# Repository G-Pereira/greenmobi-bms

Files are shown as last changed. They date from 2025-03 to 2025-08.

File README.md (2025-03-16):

# GreenMobi BMS - A BMS board compatible with the VESC BMS firmware

The [VESC BMS board system is under closed development](https://vesc-project.com/node/311) at the time of this writing although the BMS firmware is publicly available so this project consists on a VESC compatible BMS board that is able to run [VESC BMS firmware](https://github.com/vedderb/vesc_express).

This project is under development and the board is not yet ready. [KiCAD](https://www.kicad.org/) is being used for the board's design and contributions are welcome.

[**Join us on discord**](https://discord.gg/AxKemSxhaV)

## Desing approach

Since there is not yet a opensource design of a VESC fully compatible BMS this board is being designed with ease of development in mind so it can be used as a reference design to contribute directly to the VESC project and extend its potential. So the following principles are followed:

- Popular and easy to source connectors are used (JST PH, screw terminals, etc) even if in most end uses it would be better to have weatherproof panel connectors.
- SMD packages optimized for JLC assembly or PnP on premises (down to 0402 passives).
- Up to 32S supported

Here it is a block diagram of the design:

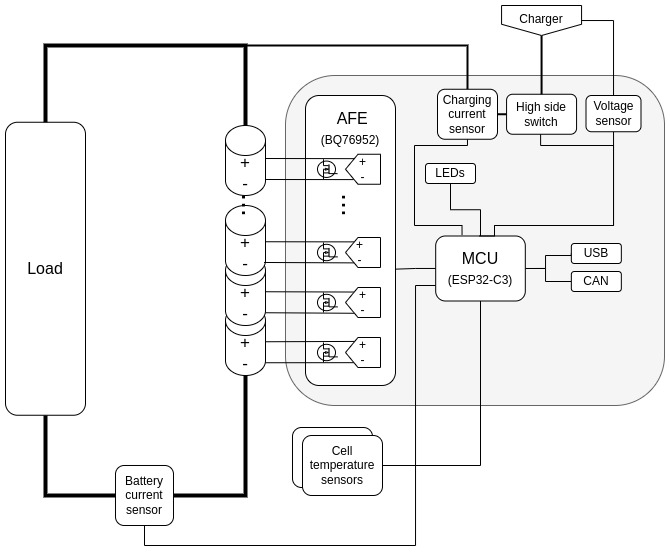
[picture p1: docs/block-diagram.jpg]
Block diagram


## Contributions

Since the design is at a schematic phase, it would be helpful if you can review the board's schematic to look for misconnections and erros using any of the given ICs. However, any other kind of productive feedback and work is welcome. Be sure to read the [design approach](#desing-approach) so your contributions match the goals of the project.

### Schematic PDF

To get the latest PDF version of the shematic go to GitHub Actions and download the artifacts of the latest workflow run.

## Credits

This project is meant to be interoperable with the VESC, which is a [registred trademark](https://vesc-project.com/trademark_policies), held by Benjamin Vedder and the BMS firmware and its hardware design hints that are in it that this designs follows are of Benjamin Vedder's authoring.

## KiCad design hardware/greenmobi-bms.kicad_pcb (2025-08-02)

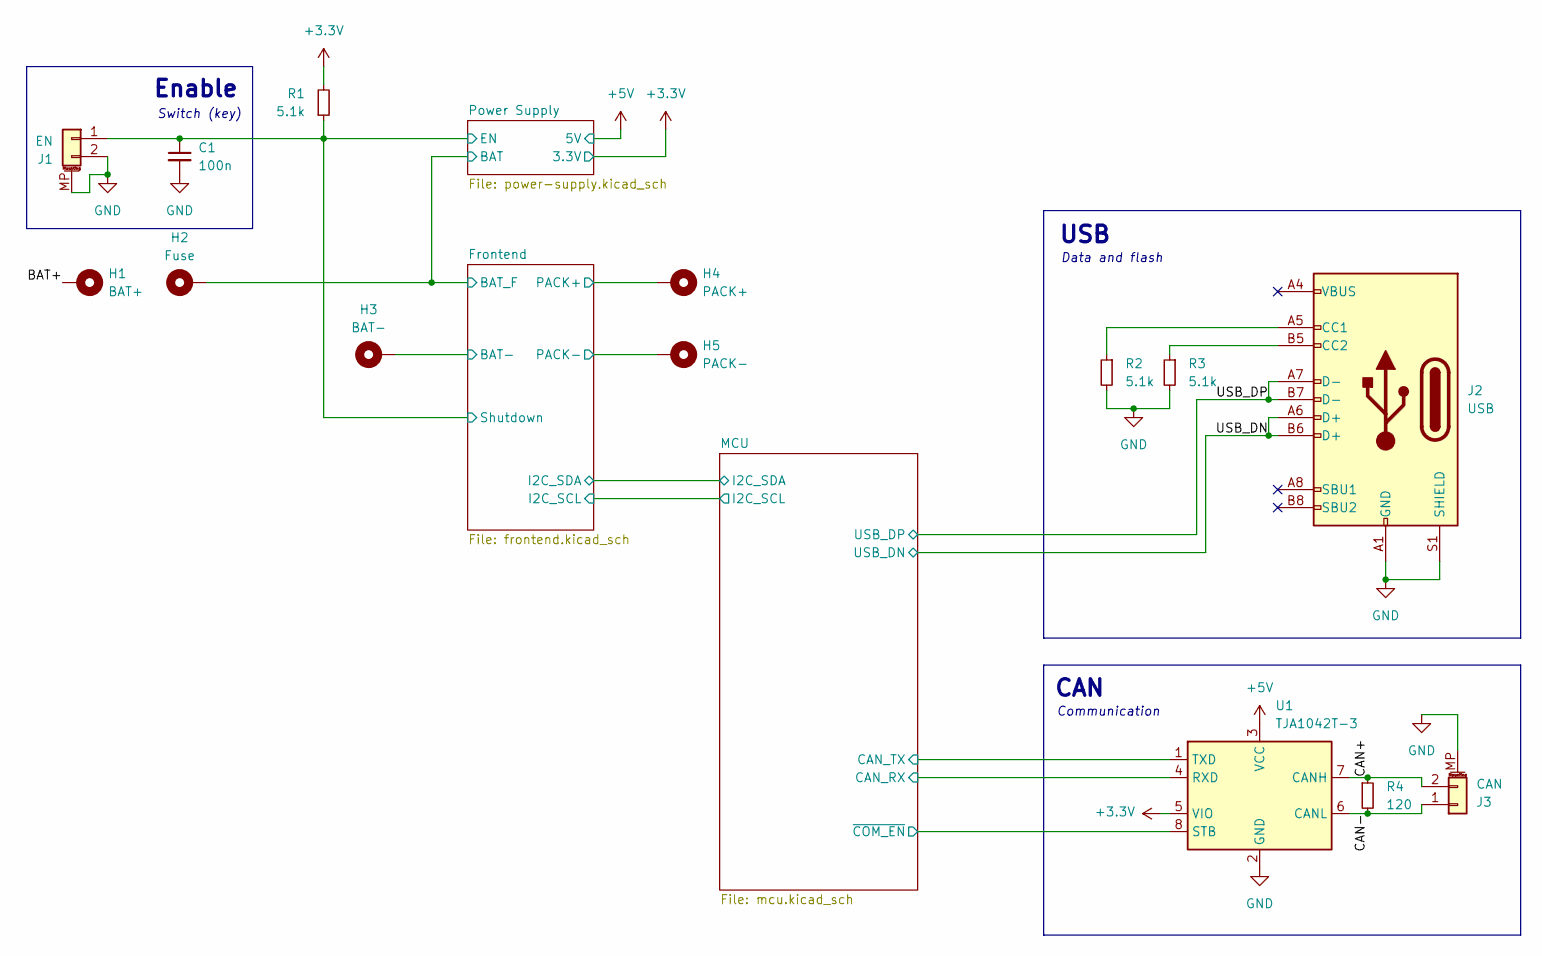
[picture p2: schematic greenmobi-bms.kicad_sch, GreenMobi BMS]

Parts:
C1: 100n; C_0402_1005Metric
H1: BAT+; Automotive_Fuse
H2: Fuse; Automotive_Fuse
H3: BAT-; Automotive_Fuse
H4: PACK+; Automotive_Fuse
H5: PACK-; Automotive_Fuse
J1: EN; JST_GH_SM02B-GHS-TB_1x02-1MP_P1.25mm_Horizontal
J2: USB; USB_C_Receptacle_Palconn_UTC16-G
J3: CAN; JST_GH_SM02B-GHS-TB_1x02-1MP_P1.25mm_Horizontal
R1, R2, R3: 5.1k; R_0402_1005Metric
R4: 120; R_0402_1005Metric
U1: TJA1042T-3; SOIC-8_3.9x4.9mm_P1.27mm; LCSC C132227

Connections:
+3.3V: R1.2, U1.5 (VIO); also elsewhere on the board
+5V: U1.3 (VCC); also elsewhere on the board
/BAT+: H1.1
/CAN+: J3.2, R4.1, U1.7 (CANH)
/CAN-: J3.1, R4.2, U1.6 (CANL)
/Frontend/BAT-: H3.1; also elsewhere on the board
/Frontend/BAT_F: H2.1; also elsewhere on the board
/Frontend/PACK+: H4.1; also elsewhere on the board
/Frontend/PACK-: H5.1; also elsewhere on the board
/Frontend/Shutdown: C1.1, J1.1, R1.1; also elsewhere on the board
/MCU/CAN_RX: U1.4 (RXD); also elsewhere on the board
/MCU/CAN_TX: U1.1 (TXD); also elsewhere on the board
/MCU/~COM_EN: U1.8 (STB); also elsewhere on the board
/USB_DN: J2.A6 (D+), J2.B6 (D+); also elsewhere on the board
/USB_DP: J2.A7 (D-), J2.B7 (D-); also elsewhere on the board
GND: C1.2, J1.2, J1.MP (MountPin), J2.A1 (GND), J2.A12 (GND), J2.B1 (GND), J2.B12 (GND), J2.S1 (SHIELD), J3.MP (MountPin), R2.2, R3.2, U1.2 (GND); also elsewhere on the board
unnamed: J2.A5 (CC1), R2.1
unnamed: J2.B5 (CC2), R3.1

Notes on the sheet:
Data and flash
Communication
CAN
Enable
USB
Switch (key)

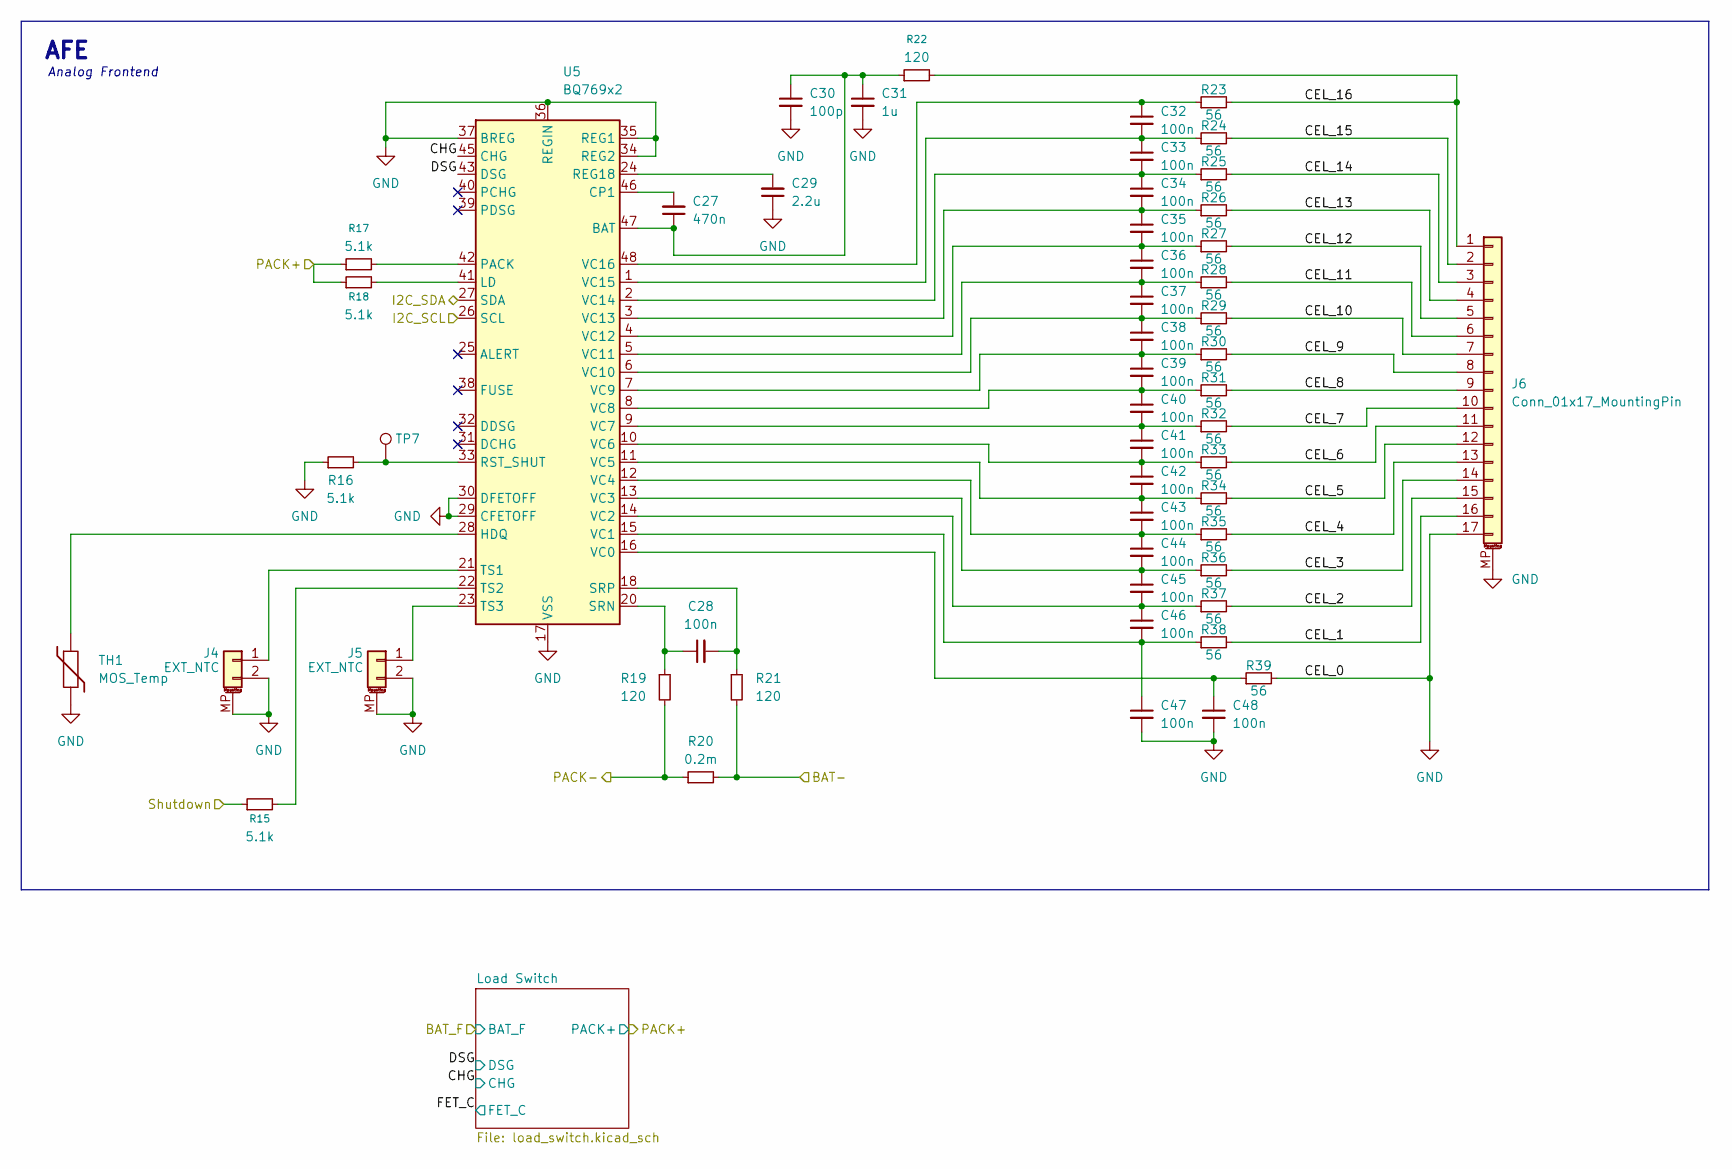
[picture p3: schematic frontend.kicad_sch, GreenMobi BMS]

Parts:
C27: 470n; C_0603_1608Metric
C28, C32, C33, C34, C35, C36, C37, C38, C39, C40, C41, C42, C43, C44, C45, C46, C47, C48: 100n; C_0402_1005Metric
C29: 2.2u; C_0603_1608Metric
C30: 100p; C_0603_1608Metric
C31: 1u; C_1206_3216Metric
J4, J5: EXT_NTC; JST_GH_SM02B-GHS-TB_1x02-1MP_P1.25mm_Horizontal
J6: Conn_01x17_MountingPin; JST_GH_SM17B-GHS-TB_1x17-1MP_P1.25mm_Horizontal; LCSC C20617492
R15, R16, R17, R18: 5.1k; R_0402_1005Metric
R19, R21, R22: 120; R_0402_1005Metric
R20: 0.2m; R_Shunt_Vishay_WSR2_WSR3; LCSC C4126121
R23, R24, R25, R26, R27, R28, R29, R30, R31, R32, R33, R34, R35, R36, R37, R38, R39: 56; R_1206_3216Metric; LCSC C2933788
TH1: MOS_Temp; R_0402_1005Metric
TP7: TestPoint; TestPoint_Pad_D1.0mm
U5: BQ769x2; TQFP-48_7x7mm_P0.5mm

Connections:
/Frontend/BAT-: R20.2, R21.2; also elsewhere on the board
/Frontend/CEL_1: J6.16, R38.2
/Frontend/CEL_2: J6.15, R37.2
/Frontend/CEL_3: J6.14, R36.2
/Frontend/CEL_4: J6.13, R35.2
/Frontend/CEL_5: J6.12, R34.2
/Frontend/CEL_6: J6.11, R33.2
/Frontend/CEL_7: J6.10, R32.2
/Frontend/CEL_8: J6.9, R31.2
/Frontend/CEL_9: J6.8, R30.2
/Frontend/CEL_10: J6.7, R29.2
/Frontend/CEL_11: J6.6, R28.2
/Frontend/CEL_12: J6.5, R27.2
/Frontend/CEL_13: J6.4, R26.2
/Frontend/CEL_14: J6.3, R25.2
/Frontend/CEL_15: J6.2, R24.2
/Frontend/CEL_16: J6.1, R22.2, R23.2
/Frontend/CHG: U5.45 (CHG); also elsewhere on the board
/Frontend/DSG: U5.43 (DSG); also elsewhere on the board
/Frontend/I2C_SCL: U5.26 (SCL); also elsewhere on the board
/Frontend/I2C_SDA: U5.27 (SDA); also elsewhere on the board
/Frontend/PACK+: R17.1, R18.1; also elsewhere on the board
/Frontend/PACK-: R19.2, R20.1; also elsewhere on the board
/Frontend/Shutdown: R15.1; also elsewhere on the board
GND: C29.1, C30.2, C31.2, C47.2, C48.2, J4.2, J4.MP (MountPin), J5.2, J5.MP (MountPin), J6.17, J6.MP (MountPin), R16.1, R39.2, TH1.2, U5.17 (VSS), U5.29 (CFETOFF), U5.30 (DFETOFF), U5.34 (REG2), U5.35 (REG1), U5.36 (REGIN), U5.37 (BREG); also elsewhere on the board
unnamed: J4.1, U5.21 (TS1)
unnamed: J5.1, U5.23 (TS3)
unnamed: C27.1, C30.1, C31.1, R22.1, U5.47 (BAT)
unnamed: C27.2, U5.46 (CP1)
unnamed: TH1.1, U5.28 (HDQ)
unnamed: R18.2, U5.41 (LD)
unnamed: R17.2, U5.42 (PACK)
unnamed: C29.2, U5.24 (REG18)
unnamed: R16.2, TP7.1, U5.33 (RST_SHUT)
unnamed: C28.1, R19.1, U5.20 (SRN)
unnamed: C28.2, R21.1, U5.18 (SRP)
unnamed: R15.2, U5.22 (TS2)
unnamed: C48.1, R39.1, U5.16 (VC0)
unnamed: C46.2, C47.1, R38.1, U5.15 (VC1)
unnamed: C45.2, C46.1, R37.1, U5.14 (VC2)
unnamed: C44.2, C45.1, R36.1, U5.13 (VC3)
unnamed: C43.2, C44.1, R35.1, U5.12 (VC4)
unnamed: C42.2, C43.1, R34.1, U5.11 (VC5)
unnamed: C41.2, C42.1, R33.1, U5.10 (VC6)
unnamed: C40.2, C41.1, R32.1, U5.9 (VC7)
unnamed: C39.2, C40.1, R31.1, U5.8 (VC8)
unnamed: C38.2, C39.1, R30.1, U5.7 (VC9)
unnamed: C37.2, C38.1, R29.1, U5.6 (VC10)
unnamed: C36.2, C37.1, R28.1, U5.5 (VC11)
unnamed: C35.2, C36.1, R27.1, U5.4 (VC12)
unnamed: C34.2, C35.1, R26.1, U5.3 (VC13)
unnamed: C33.2, C34.1, R25.1, U5.2 (VC14)
unnamed: C32.2, C33.1, R24.1, U5.1 (VC15)
unnamed: C32.1, R23.1, U5.48 (VC16)

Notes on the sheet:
Analog Frontend
AFE

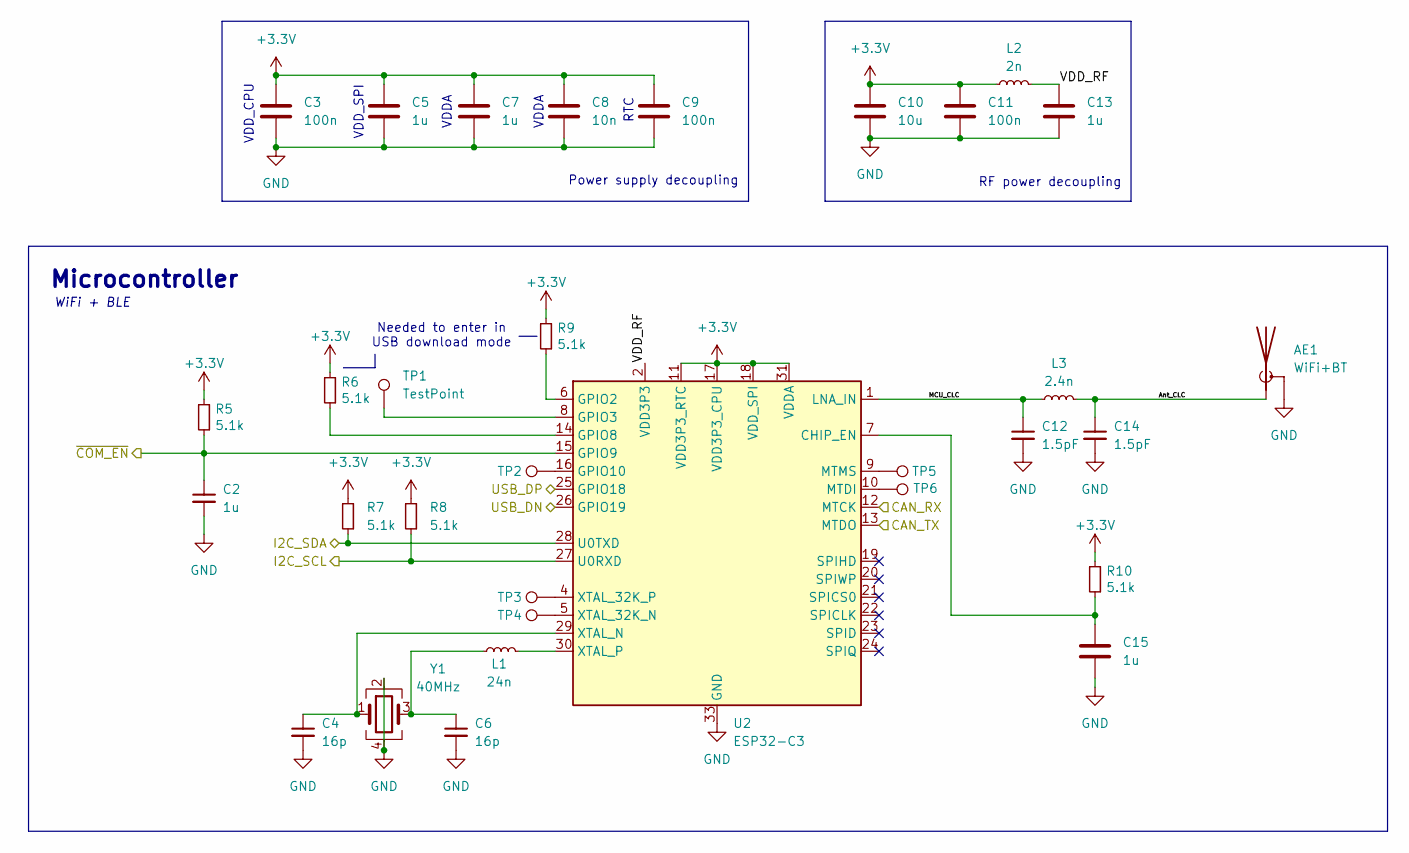
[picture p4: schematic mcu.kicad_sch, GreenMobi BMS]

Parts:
AE1: WiFi+BT; Texas_SWRA117D_2.4GHz_Right
C2, C5, C7, C13, C15: 1u; C_0402_1005Metric
C3, C9, C11: 100n; C_0402_1005Metric
C4, C6: 16p; C_0402_1005Metric
C8: 10n; C_0402_1005Metric
C10: 10u; C_0402_1005Metric
C12, C14: 1.5pF; C_0402_1005Metric; LCSC C282238
L1: 24n; L_0402_1005Metric
L2: 2n; L_0402_1005Metric
L3: 2.4n; L_0402_1005Metric; LCSC C97997
R5, R6, R7, R8, R9, R10: 5.1k; R_0402_1005Metric
TP1, TP2, TP3, TP4, TP5, TP6: TestPoint; TestPoint_Pad_D1.0mm
U2: ESP32-C3; QFN-32-1EP_5x5mm_P0.5mm_EP3.7x3.7mm_ThermalVias; LCSC C2858491
Y1: 40MHz; Crystal_SMD_2520-4Pin_2.5x2.0mm; LCSC C3007519

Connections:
+3.3V: C3.1, C5.1, C7.1, C8.1, C9.1, C10.1, C11.1, L2.1, R5.1, R6.1, R7.1, R8.1, R9.1, R10.1, U2.11 (VDD3P3_RTC), U2.17 (VDD3P3_CPU), U2.18 (VDD_SPI), U2.31 (VDDA), U2.32 (VDDA); also elsewhere on the board
/Frontend/I2C_SCL: R8.2, U2.27 (U0RXD); also elsewhere on the board
/Frontend/I2C_SDA: R7.2, U2.28 (U0TXD); also elsewhere on the board
/MCU/Ant_CLC: AE1.1 (A), C14.1, L3.2
/MCU/CAN_RX: U2.12 (MTCK); also elsewhere on the board
/MCU/CAN_TX: U2.13 (MTDO); also elsewhere on the board
/MCU/MCU_CLC: C12.1, L3.1, U2.1 (LNA_IN)
/MCU/VDD_RF: C13.1, L2.2, U2.2 (VDD3P3), U2.3 (VDD3P3)
/MCU/~COM_EN: C2.1, R5.2, U2.15 (GPIO9); also elsewhere on the board
/USB_DN: U2.26 (GPIO19); also elsewhere on the board
/USB_DP: U2.25 (GPIO18); also elsewhere on the board
GND: AE1.2 (Shield), C2.2, C3.2, C4.2, C5.2, C6.2, C7.2, C8.2, C9.2, C10.2, C11.2, C12.2, C13.2, C14.2, C15.2, U2.33 (GND), Y1.2, Y1.4; also elsewhere on the board
unnamed: C6.1, L1.1, Y1.3
unnamed: C15.1, R10.2, U2.7 (CHIP_EN)
unnamed: R9.2, U2.6 (GPIO2)
unnamed: TP1.1, U2.8 (GPIO3)
unnamed: R6.2, U2.14 (GPIO8)
unnamed: TP2.1, U2.16 (GPIO10)
unnamed: TP6.1, U2.10 (MTDI)
unnamed: TP5.1, U2.9 (MTMS)
unnamed: TP4.1, U2.5 (XTAL_32K_N)
unnamed: TP3.1, U2.4 (XTAL_32K_P)
unnamed: C4.1, U2.29 (XTAL_N), Y1.1
unnamed: L1.2, U2.30 (XTAL_P)

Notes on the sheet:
VDD_SPI
VDD_CPU
WiFi + BLE
RTC
Power supply decoupling
VDDA
Microcontroller
RF power decoupling
Needed to enter in USB download mode

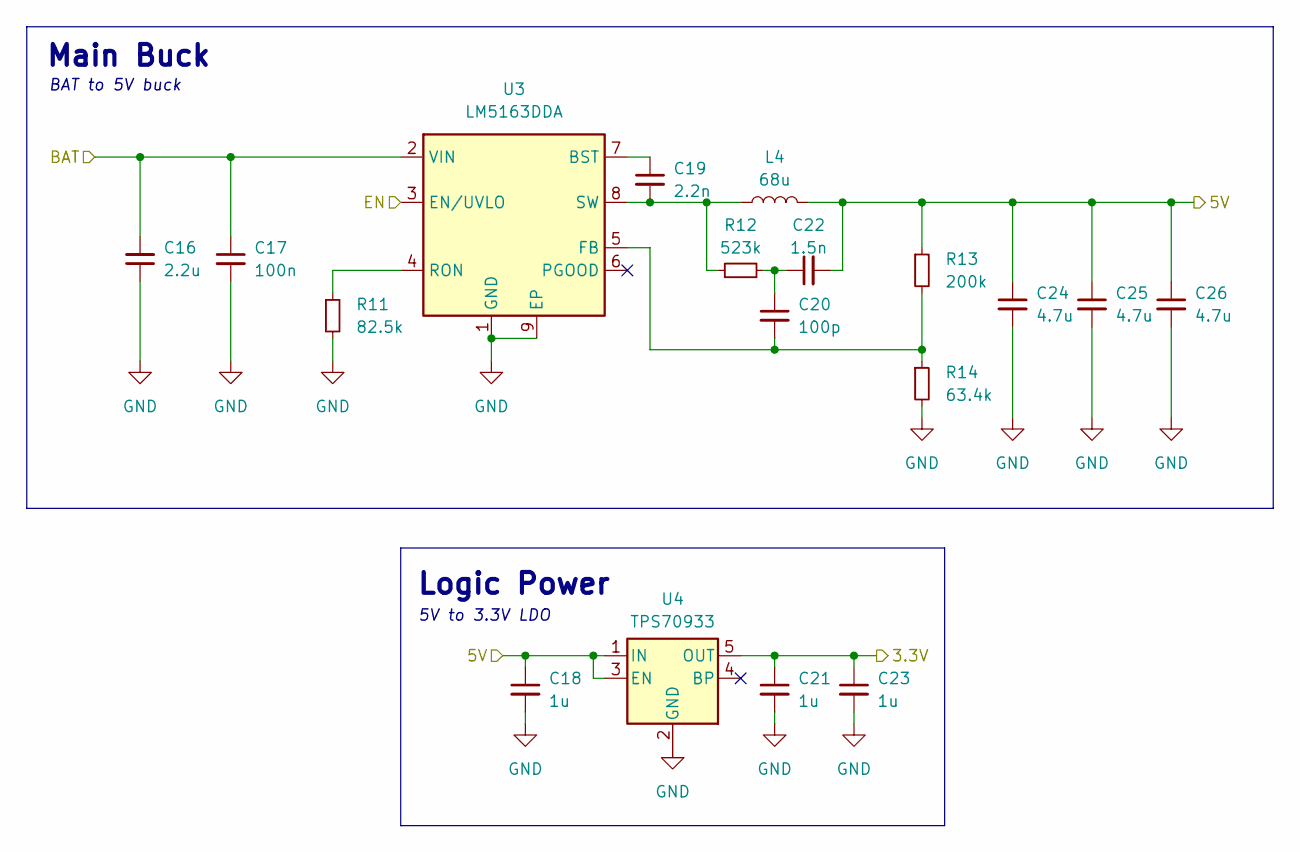
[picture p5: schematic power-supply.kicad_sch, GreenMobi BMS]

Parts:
C16: 2.2u; C_1206_3216Metric; LCSC C577211
C17: 100n; C_1206_3216Metric; LCSC C1945
C18, C21, C23: 1u; C_0402_1005Metric
C19: 2.2n; C_0402_1005Metric; LCSC C106861
C20: 100p; C_0603_1608Metric
C22: 1.5n; C_0603_1608Metric
C24, C25, C26: 4.7u; C_0805_2012Metric
L4: 68u; L_KOHERelec_MDA7030; LCSC C2894721
R11: 82.5k; R_0402_1005Metric
R12: 523k; R_0402_1005Metric
R13: 200k; R_0402_1005Metric
R14: 63.4k; R_0402_1005Metric
U3: LM5163DDA; HSOP-8-1EP_3.9x4.9mm_P1.27mm_EP2.41x3.1mm_ThermalVias; LCSC C2873264
U4: TPS70933; SOT-23-5; LCSC C89347

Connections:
+3.3V: C21.1, C23.1, U4.5 (OUT); also elsewhere on the board
+5V: C18.1, C22.2, C24.1, C25.1, C26.1, L4.2, R13.1, U4.1 (IN), U4.3 (EN); also elsewhere on the board
/Frontend/BAT_F: C16.2, C17.1, U3.2 (VIN); also elsewhere on the board
/Frontend/Shutdown: U3.3 (EN/UVLO); also elsewhere on the board
GND: C16.1, C17.2, C18.2, C21.2, C23.2, C24.2, C25.2, C26.2, R11.2, R14.2, U3.1 (GND), U3.9 (EP), U4.2 (GND); also elsewhere on the board
unnamed: C20.1, C22.1, R12.2
unnamed: C19.1, U3.7 (BST)
unnamed: C20.2, R13.2, R14.1, U3.5 (FB)
unnamed: R11.1, U3.4 (RON)
unnamed: C19.2, L4.1, R12.1, U3.8 (SW)

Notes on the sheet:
Logic Power
5V to 3.3V LDO
Main Buck
BAT to 5V buck

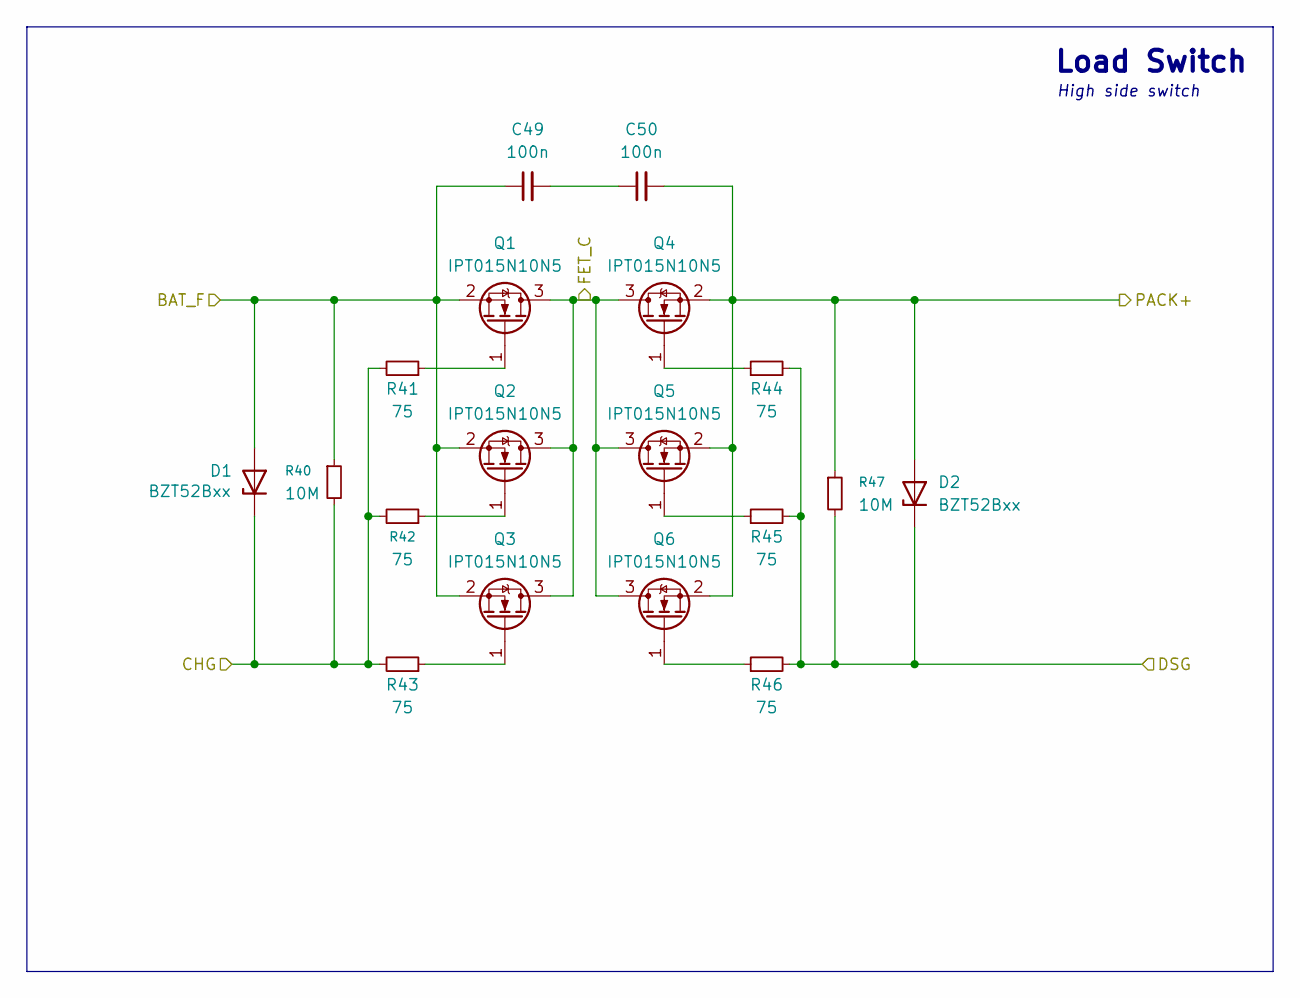
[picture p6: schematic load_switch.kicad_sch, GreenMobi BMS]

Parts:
C49, C50: 100n; C_1206_3216Metric; LCSC C1945
D1, D2: BZT52Bxx; D_SOD-123F
Q1, Q2, Q3, Q4, Q5, Q6: IPT015N10N5; Infineon_PG-HSOF-8-1_ThermalVias; LCSC C108964
R40, R47: 10M; R_0402_1005Metric
R41, R42, R43, R44, R45, R46: 75; C_0402_1005Metric

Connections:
/Frontend/BAT_F: C49.1, D1.2 (A), Q1.2 (S), Q2.2 (S), Q3.2 (S), R40.1; also elsewhere on the board
/Frontend/CHG: D1.1 (K), R40.2, R41.2, R42.2, R43.2; also elsewhere on the board
/Frontend/DSG: D2.1 (K), R44.2, R45.2, R46.2, R47.2; also elsewhere on the board
/Frontend/FET_C: Q1.3 (D), Q2.3 (D), Q3.3 (D), Q4.3 (D), Q5.3 (D), Q6.3 (D)
/Frontend/PACK+: C50.2, D2.2 (A), Q4.2 (S), Q5.2 (S), Q6.2 (S), R47.1; also elsewhere on the board
unnamed: C49.2, C50.1
unnamed: Q1.1 (G), R41.1
unnamed: Q2.1 (G), R42.1
unnamed: Q3.1 (G), R43.1
unnamed: Q4.1 (G), R44.1
unnamed: Q5.1 (G), R45.1
unnamed: Q6.1 (G), R46.1

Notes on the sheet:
Load Switch
High side switch

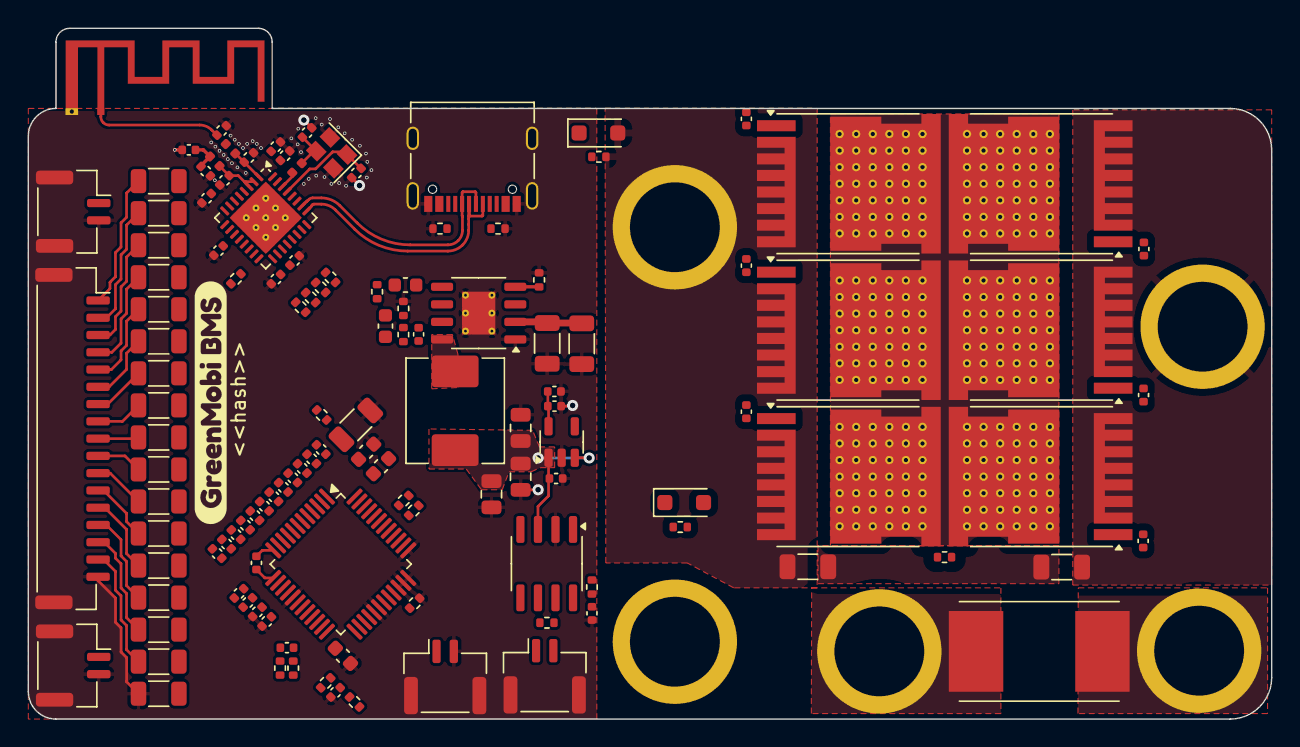
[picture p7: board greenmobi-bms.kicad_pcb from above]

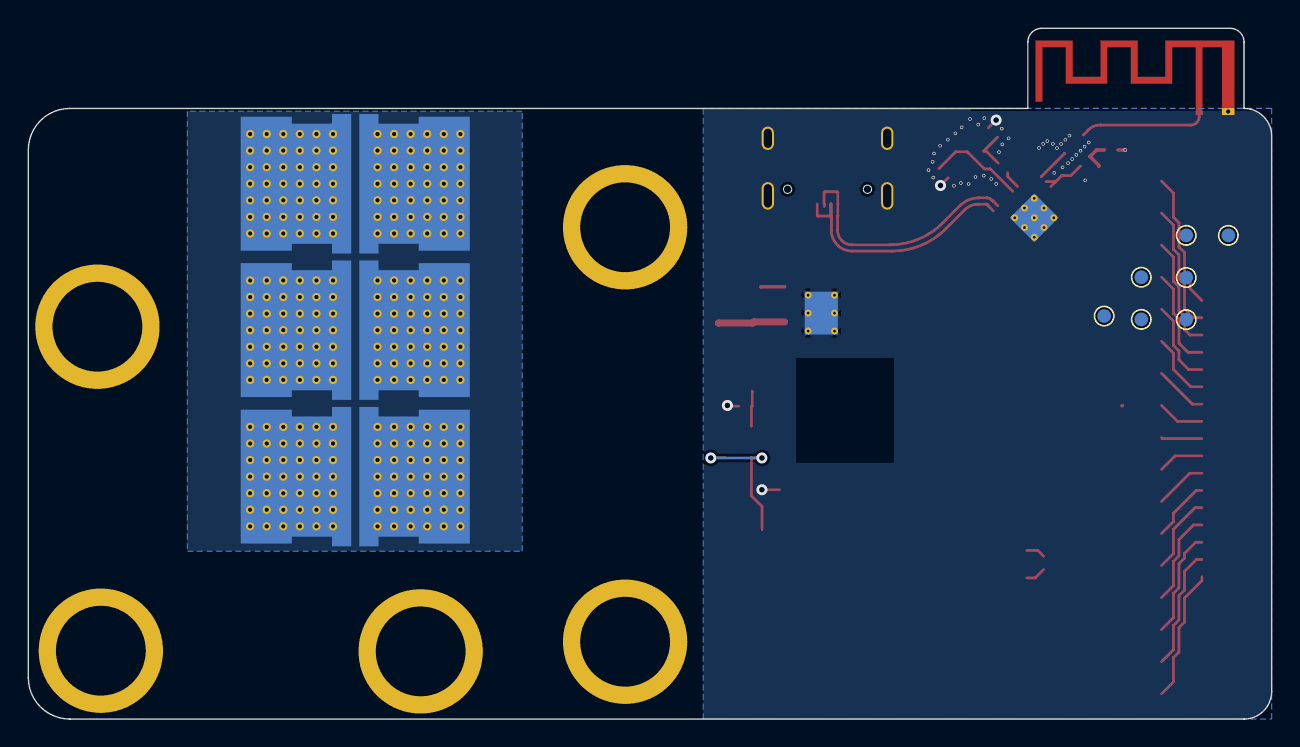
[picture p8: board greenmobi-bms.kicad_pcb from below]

Board: 4 copper layers, 90.0 x 50.0 mm, 136 parts (7 on the bottom side), 94 nets.

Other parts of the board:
kibuzzard-688328D2: G***; kibuzzard-688328D2

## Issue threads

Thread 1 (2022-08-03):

Your LTC6811 SPI interface pinout does not correspond with Vesc FW

Kabron287, 2022-08-03:
Hi, there
I flash 1**2s7p\vesc_default.bin** from Vesc BMS github to Nucleo-F476 board and find it works.
But it doesn't work with LTC6811 board if I use SPI pinout from your schematic.
I rewired SPI according Ennoid BMS schematic and now it works with Vesc Tool SW.

Correct pinout is:
PA4 - SS
PA5 - SCK
PA6 - MISO
PA7 - MOSI

G-Pereira, 2022-08-03:
Hey @Kabron287 ! Thank you for your feedback. I have not crossed that board design when I did my research. That's exactly and I was aiming for on a second iteration of this project.
Do you think I can develop this project in a different direction than the Ennoid BMS which would be a good alternative? I don't have any reason to work on a board that will have the exact features of one that already is opensource.

Kabron287, 2022-08-03:
> Do you think I can develop this project in a different direction than the Ennoid BMS which would be a good alternative?
Of course you can.
I guess it'll depend of the level of compatibility with Vesc FW if you do not wish to rewrite official FW or develop your own.

G-Pereira, 2022-08-03:
I am aiming for complete compatibility not just because it would require me less work but most importantly so we can centralize efforts and contribute to the project and make it grow which would be better not only for me that I am using it but also for Benjamin, Trampa and all other people using this ecosystem.

Kabron287, 2022-08-03:
So, you have to change pinout, I guess.

G-Pereira, 2022-08-03:
I am not sure because I am following the `hwconf/hw_rbat.h` and you are not using an MCU from the same STM32 line. I am using the STM32L476 at the moment.

Kabron287, 2022-08-03:
Sorry, my board is NUCLEO-L476RG

G-Pereira, 2022-08-03:
Ah ok! That makes sense, you would need to compile with the pins I am using. But I will check which SPI pins I will choose. For now I am using the `hw_rabat.h` just to connect things as I go just to check the amount of pins I have available I will do a careful pin assignment once I am done with all sub circuits.

G-Pereira, 2022-08-03:
I've close this for now because it isn't exactly an issue but I would like to continue the conversation on Discord, I've noticed you've joined us there!

Closed 2022-08-03.

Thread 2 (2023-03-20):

Submit LTC6813 to KiCAD libraries

G-Pereira, 2023-03-20:
Submit the symbol and footprint to KiCAD libraries. This will also help to get the files peer reviewed before ordering PCBs
https://gitlab.com/kicad/libraries/kicad-symbols
https://gitlab.com/kicad/libraries/kicad-footprints

G-Pereira, 2024-01-26:
Do the same for LTC6820

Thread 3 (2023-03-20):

Split design into two boards

G-Pereira, 2023-03-20:
Having a front-end board and a controller board allows one board to connect to several front-ends or reuse the controller between setups (not have to design the controller part for each cell series arrangements)

G-Pereira, 2023-10-10:
When parallelization is needed (multiple AFEs) to a single MCU it is far better to link them via CAN bringing segmentation and a better fault tolerant design. So this will not be pursued

G-Pereira, 2023-12-07:
We went back on this decision and we have split the design into two boards since this is not meant to add battery packs in parallel but instead have the flexibility to make batteries with more than 18 series connections.

Closed 2023-10-10.

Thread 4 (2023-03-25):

E73-2G4M08S1C is not a good idea

Kabron287, 2023-03-25:
It is BLE chip.
Windows does not work with BLE.
You will not be able to use Vesc/Ennoid tools.

You should use any Bluetooth SPP chip.

G-Pereira, 2023-03-25:
Hi @Kabron287, thank you for your feedback.
This BLE module will be used to connect to mobile phones, hand held controllers (ex. joysticks) and other data logging/display devices. For example we can use this as well to monitor battery packs in storage units which discharge over time and need to be recharged an alert is sent via a BLE gateway) for large scale management of battery packs.

For the moment, to achieve the feature you suggest we are considering using the expansion header to connect a Bluetooth radio.

I'll keep this issue open until the block diagram is amended to state BLE instead of Bluetooth.

Kabron287, 2023-03-25:
You Boss. You responce.

G-Pereira, 2023-04-08:
Changes made. Thank you!

Closed 2023-04-08.

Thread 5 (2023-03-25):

MCP2562 alternative

Kabron287, 2023-03-25:
In our design we use ADM3053BRWZ.
It has galvanic isolation with internal DC/DC converter.

G-Pereira, 2023-03-25:
Hi @Kabron287, thank you for reviewing the design! It is very appreciated.

Our CAN bus will be used to establish data links between the BMS, motor controller and in the future our pedals, head unit and others. All those systems will be powered from the vehicle power bus so galvanic isolation would have no use here.

However, to protect external equipment we should recommend that an isolated CAN transceiver is used in those cases.

Closed 2023-03-25.

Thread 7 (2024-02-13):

Replace AMS1117 with power efficient solution

G-Pereira, 2024-02-13:

G-Pereira, 2024-02-15:
Replaced with TPS7A0533

Closed 2024-02-15.

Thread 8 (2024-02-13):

Increase Schematic redability

G-Pereira, 2024-02-13:
Avoid using so much hierarchy

G-Pereira, 2024-02-13:
Thank you @davidmolony and @pinski1 for the suggestion!

G-Pereira, 2024-02-14:
Schematic is now much more readable!

Closed 2024-02-14.

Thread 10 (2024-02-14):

Check that analog signals are connected to MCU ADC capable pins

G-Pereira, 2024-02-14:
Thanks @davidmolony !

G-Pereira, 2025-04-16:
Analog signals moved to AFE IC so ADC from MCU is no longer being used.

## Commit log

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2022-07-31 Added AFE chip symbol
    [afe.kicad_sch, vesc-bms.kicad_sch]
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2022-07-31 Added footprints and some LCSC part numbers
    [afe.kicad_sch, mcu.kicad_sch, vesc-bms.kicad_sch]
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2022-07-31 Some work on Battery AFE and PSU
    [afe.kicad_sch, comms.kicad_sch, power-supply.kicad_sch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]
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2022-07-31 Analog front end daisy chain
    [afe.kicad_sch, balance_front_end.kicad_sch, comms.kicad_sch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]
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2022-07-31 Analog front end ready
    [afe.kicad_sch, balance_front_end.kicad_sch, comms.kicad_sch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]
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2022-08-01 Fix schematic
    [vesc-bms.kicad_sch]
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2022-11-10 MicroFit 3.0 for battery connector
    [afe.kicad_sch, vesc-bms.kicad_sch]
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2023-03-20 Update design to KiCAD v7
    [afe.kicad_sch, balance_front_end.kicad_sch, comms.kicad_sch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]
2023-03-20 DNP marks from new KiCAD
    [afe.kicad_sch, balance_front_end.kicad_sch]
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2023-04-25 Initial work on High side switch
    [charger_monitoring.kicad_sch]
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2023-04-29 Charger enable circiut and more ext NTC
    [charger_monitoring.kicad_sch, ntc.kicad_sch, thermal.kicad_sch]
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2023-04-29 Remove left over IC
    [comms.kicad_sch]
2023-04-29 Improve AFE power supply filtering
    [afe.kicad_sch, balance_front_end.kicad_sch]
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2023-10-10 Total current sense and buzzer
    [afe.kicad_sch, balance_front_end.kicad_sch, charger_monitoring.kicad_sch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]
2023-10-10 Fuse in balancing circuit
    [balance_front_end.kicad_sch]
2023-12-07 Split the design into front end and controller
    [afe.kicad_sch, balance_front_end.kicad_sch, ble.kicad_sch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]
2023-12-13 Set IBIAS resistors for daisy chain
    [balance_front_end.kicad_sch, greenmobi-bms-frontend.kicad_sch]
2023-12-13 Filter frontend input voltage
    [balance_front_end.kicad_sch, greenmobi-bms-frontend.kicad_sch]
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2024-01-29 Current sensors and ISOSPI interface
    [charger_monitoring.kicad_sch, greenmobi-bms-controller.kicad_sch, isospi_interface.kicad_sch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]
2024-02-08 Changed back to a unified design
    [afe.kicad_sch, balance_front_end.kicad_sch, ble.kicad_sch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]
2024-02-08 Fix OLED pinout and add HDC1080
    [balance_front_end.kicad_sch, charger_monitoring.kicad_sch, frontend.kicad_sch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]
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2024-02-09 Wire up the AFE
    [balance_front_end.kicad_sch, frontend.kicad_sch, greenmobi-bms.kicad_sch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]
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2024-02-09 BAT to 12V converter
    [balance_front_end.kicad_sch, charger_monitoring.kicad_sch, comms.kicad_sch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]
2024-02-09 Add missing files
    [balance_front_end.kicad_sch, power-supply.kicad_sch]
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2024-02-09 Add option to power AFE from 5V on board regulator
    [frontend.kicad_sch, greenmobi-bms.kicad_sch]
2024-02-10 Fix some ERC issues
    [balance_front_end.kicad_sch, charger_monitoring.kicad_sch, comms.kicad_sch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]
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2024-02-13 Remove BLE module to increase efficiency
    [balance_front_end.kicad_sch, charger_monitoring.kicad_sch, comms.kicad_sch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]
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2024-02-13 Fix orientation of balance FET
    [balance_front_end.kicad_sch]
2024-02-13 Change LEDs to 3mm
    [mcu.kicad_sch]
2024-02-14 Fix AFE readability
    [balance_front_end.kicad_sch, ble.kicad_sch, charger_monitoring.kicad_sch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]
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2024-02-14 Fix redability issues
    [frontend.kicad_sch, greenmobi-bms.kicad_sch, thermistor.kicad_sch]
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2024-02-15 Add switch to current sensors
    [charger_monitoring.kicad_sch, greenmobi-bms.kicad_sch, mcu.kicad_sch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]
2024-02-15 Replaced LDO
    [power-supply.kicad_sch]
2024-02-16 Replace buck regulator
    [power-supply.kicad_sch]
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2024-03-28 Update to KiCAD 8
    [charger_monitoring.kicad_sch, frontend.kicad_sch, greenmobi-bms.kicad_sch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]
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2024-03-29 Tune Charger current and MOSFET fix orientation
    [charger_monitoring.kicad_sch, frontend.kicad_sch, greenmobi-bms.kicad_sch]
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2024-03-30 Ongoing work on high side switch
    [charger_monitoring.kicad_sch, greenmobi-bms.kicad_sch]
2024-10-17 Changed MCU and AFE
    [charger_monitoring.kicad_sch, frontend.kicad_sch, greenmobi-bms.kicad_sch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]
2024-10-20 Some work on AFE
    [frontend.kicad_sch]
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2024-10-21 Connect AFE IC to Balance connector
    [frontend.kicad_sch]
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2024-10-22 fix bom JLC
2024-10-22 added outline to avoid BOM generation fail
    [greenmobi-bms.kicad_pcb]
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2024-10-31 Cell balancing of 32S
    [frontend.kicad_sch]
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2024-11-04 Level shifting for sync between top and bot AFE
    [frontend.kicad_sch, greenmobi-bms.kicad_pcb]
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2024-11-06 CI fix PCB upload
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2024-11-20 CHG and DSH circuitry
    [frontend.kicad_sch, greenmobi-bms.kicad_sch]
2024-11-22 Fix Voltage supply of AFEs
    [frontend.kicad_sch]
2025-03-10 Update to KiCAD 9
    [frontend.kicad_sch, greenmobi-bms.kicad_pcb, greenmobi-bms.kicad_sch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]
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2025-03-11 Fix CI
    [greenmobi-bms.kicad_pcb]
2025-03-11 Revert "Fix CI"
    This reverts commit 2ed332ad77608375af669dbbad6183d480b8686f.
    [greenmobi-bms.kicad_pcb]
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2025-03-13 Remove Thermal reliefs from connectors MP and ESP32 Crystal
    [cell.kicad_sch, frontend.kicad_sch, greenmobi-bms.kicad_pcb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]
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2025-03-13 Increased Discharge Resistor size
    [cell.kicad_sch, greenmobi-bms.kicad_pcb]
2025-03-13 Cell balancing sourcing and repositioning
    [cell.kicad_sch, frontend.kicad_sch, greenmobi-bms.kicad_pcb]
2025-03-15 Various changes (can't remember)
    [frontend.kicad_sch, greenmobi-bms.kicad_sch, mcu.kicad_sch]
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2025-03-16 Increased spec for 32S
    [cell.kicad_sch, frontend.kicad_sch]
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2025-03-17 Charge and Discharge FETs
    [cell.kicad_sch, frontend.kicad_sch, greenmobi-bms.kicad_pcb]
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2025-03-26 MCU circuit sourced complete
    [greenmobi-bms.kicad_pcb, greenmobi-bms.kicad_sch, mcu.kicad_sch]
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2025-04-10 Fix NTC connection
    [frontend.kicad_sch]
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2025-04-11 gate drivers open to be defined
    [frontend.kicad_sch]
2025-04-14 Reduce to 16S for now
    [cell.kicad_sch, frontend.kicad_sch, greenmobi-bms.kicad_sch]
2025-04-15 LDO changed to a low Iq
    [greenmobi-bms.kicad_sch, power-supply.kicad_sch]
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2025-04-16 Fix Schematic generated by CI
    [frontend.kicad_sch]
2025-04-16 Add missing cell conection
    [frontend.kicad_sch, mcu.kicad_sch]
2025-04-16 Change balancing to a unified connector
    [frontend.kicad_sch]
2025-04-16 Fix footprint library path
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2025-04-16 Change balance current and set most of the footprints
    [frontend.kicad_sch, greenmobi-bms.kicad_sch, mcu.kicad_sch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]
2025-04-16 Initial layout placement study
    [greenmobi-bms.kicad_pcb]
2025-04-16 Cleanup ERC errors
    [frontend.kicad_sch, greenmobi-bms.kicad_pcb, greenmobi-bms.kicad_sch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]
2025-04-16 Connectors changed to JST GH
    [frontend.kicad_sch, greenmobi-bms.kicad_pcb, greenmobi-bms.kicad_sch]
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2025-04-17 Add resistor to discharge load switches gates
    [frontend.kicad_sch, greenmobi-bms.kicad_sch, mcu.kicad_sch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]
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2025-04-18 Improvements to main buck and load switch
    [frontend.kicad_sch, greenmobi-bms.kicad_pcb, greenmobi-bms.kicad_sch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]
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2025-06-14 Replace Front end input diode for a Schotky
    [frontend.kicad_sch, greenmobi-bms.kicad_pcb, load_switch.kicad_sch]
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2025-06-14 Change MCU footprint to GND vias on EPAD
    [greenmobi-bms.kicad_pcb, mcu.kicad_sch]
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2025-06-17 Board dimensions fix
    [greenmobi-bms.kicad_pcb]
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2025-06-18 Fix Silkscreeen on PCB CI export
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2025-07-21 Fix connection
    [frontend.kicad_sch, greenmobi-bms.kicad_pcb]
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
